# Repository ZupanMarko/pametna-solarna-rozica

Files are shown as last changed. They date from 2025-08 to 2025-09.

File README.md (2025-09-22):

# Pametna solarna rožica
Projekt vključuje izvorne datoteke in programsko kodo za projekt *Pametna solarna rožica* iz Poletne šole strojništva 2025.
Gre za napravo, ki sledi soncu za optimalni izkoristek sončnih celic na vrhu. Rožica vključuje baterijo in vezje za hitro polnjenje mobilnega telefona.

<p align="center">
  
  <video src="https://github.com/user-attachments/assets/c149758f-b2a8-4514-8fbe-24bb865d2cd1" width="300" controls style="display:inline-block; vertical-align:middle;"></video>
</p>

Projekt vključuje:
* STEP datoteke sestavnih delov
* Altium in gerber datoteke tiskanin
* programsko kodo
* tabelo vseh sestavnih delov (BOM)

<p align="center">
  Untitled Diagram drawio
</p>

# Kosovnica

| Količina | Naziv | Tip / specifikacija | Opombe | Povezava |
|---|---|---|---|---|
| 1x | Solarni panel | 25 W, plastičen, 18 V | Uporaba na prostem | [link](https://a.aliexpress.com/_EzS1qQS) |
| 1x | Li-Ion celica | 18650, 3.7 V | Brez zaščite, potreben BMS | [link](https://a.aliexpress.com/_EvOZci2) |
| 1x | Arduino Nano | ATmega328P, USB Mini | Klon, 5 V | [link](https://a.aliexpress.com/_Ez3uUz9) |
| 1x | Servo motor | 9 g, 180° | Klasičen RC mikro servo | [link](https://a.aliexpress.com/_EwxFJdM) |
| 1x | Servo motor (kontinuirni) | 9 g, 360° | Kontinuirna rotacija | [link](https://a.aliexpress.com/_EwxFJdM) |
| 1x | MPPT regulator | 18 V vhod | Za polnjenje 1S baterije | [link](https://a.aliexpress.com/_EH76ZsS) |
| 1x | Boost pretvornik | DC–DC step-up | 5–12 V izhod | [link](https://a.aliexpress.com/_Ev8sKLp) |
| 1x | BMS modul | 1S (3.7 V) | Zaščita pred prenapetostjo/praznjenjem | [link](https://a.aliexpress.com/_EJhuM38) |
| 1x | USB modul | QC 3.0 fast charge | 5–12 V izhod | [link](https://a.aliexpress.com/_EI1u6Ka) |
| 4x | Fotoupor | GL5516 | 5–10 kΩ (odvisno od svetlobe) | [link](https://a.aliexpress.com/_EzRV2TM) |
| 1x | Kontaktni konektor | 2-pinski | Za povezavo napajanja | [link](https://a.aliexpress.com/_Ex5KoGA) |
| 1x | Nosilec baterije | 1x 18650 | S kabli | [link](https://a.aliexpress.com/_EykRIGO) |
| 2x | Terminal | Vijak M3 | Pritrditev žic | [link](https://a.aliexpress.com/_EGEYttG) |
| 1x | Stikalo | Mini toggle | ON/OFF | [link](https://a.aliexpress.com/_EIrwWxU) |
| 4x | Upor | 1 kΩ, 1/4 W | ±1 % | [link](https://a.aliexpress.com/_EH9VMBM) |
| 4x | Vijak | M3×16, inbus glava | | – |
| 2x | Vijak | M3×6, inbus glava | | – |
| 1x | Vijak | M4×30, inbus glava | | – |
| 4x | Matica | M3 | | – |
| 1x | Matica | M4 | | – |
| 4x | Žica tanka | 20 cm, cca. 0.2 mm² | Lahko parica iz UTP kabla | – |
| 2x | Žica srednja | 20 cm, 0.75 mm² | Lahko zvočniški kabel | – |
| 3x | Samolepilna nogica | Silikonska | Za stabilnost | – |

POTREBNA ORODJA:
* 3D tiskalnik in 0,3 kg PLA ali podobnega filamenta
* spajkalnik in spajka
* pištolica na vroče lepilo ali sekundno lepilo
* vrtalnik in sveder 8 mm

OPOMBE:
Za pripravo datotek na 3D tisk se priporoča uporaba slicerja PrusaSlicer, saj lahko direktno uvozi step datoteke.
Za naročilo obeh tiskanih se priporoča JLCPCB zaradi nizke cene in hitre dostave.

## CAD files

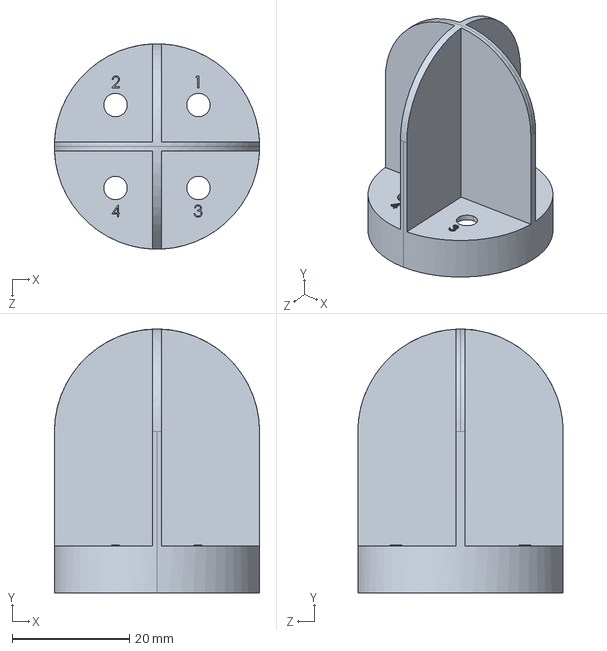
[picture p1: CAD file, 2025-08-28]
STEP datoteke/Sencnik.STEP
35.0 x 45.0 x 35.0 mm

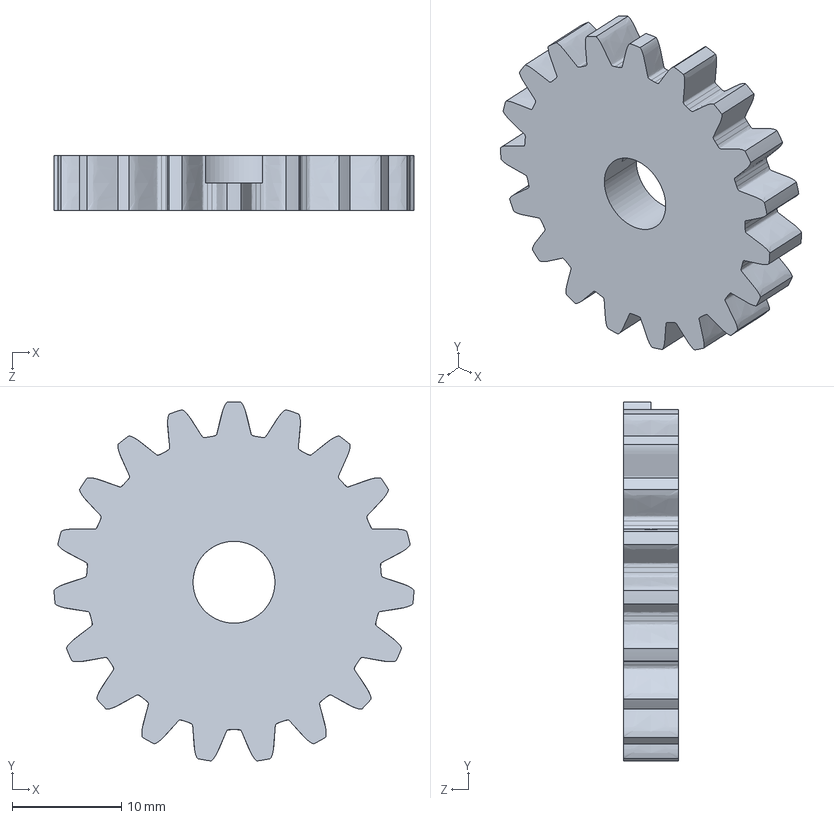
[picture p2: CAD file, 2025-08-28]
STEP datoteke/Zobnik_vrtilni.STEP
33.0 x 32.9 x 5.00 mm

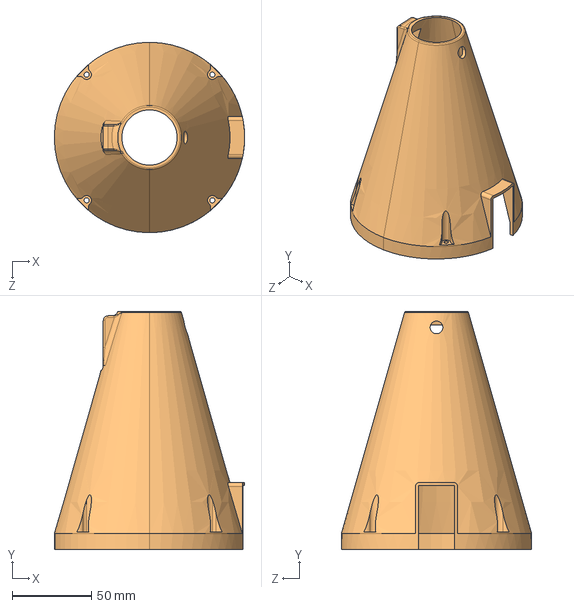
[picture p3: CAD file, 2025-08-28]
STEP datoteke/Telo.STEP
120.0 x 150.0 x 120.0 mm

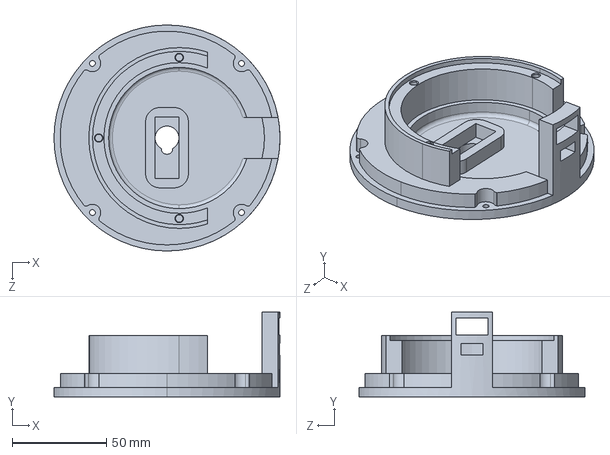
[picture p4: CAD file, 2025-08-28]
STEP datoteke/Stojalo.STEP
120.0 x 45.0 x 120.0 mm

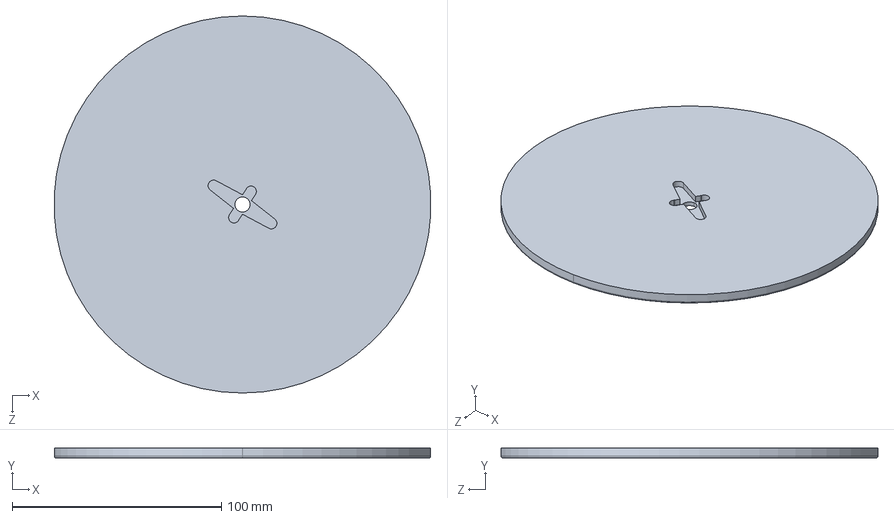
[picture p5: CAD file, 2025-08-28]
STEP datoteke/Stojisce.STEP
179.7 x 5.00 x 180.0 mm

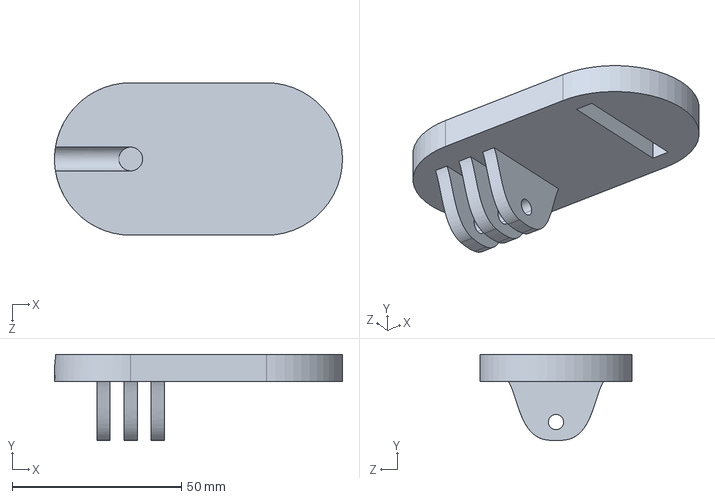
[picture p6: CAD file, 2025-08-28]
STEP datoteke/Gnani_zobnik_drzalo.STEP
85.0 x 25.5 x 45.0 mm

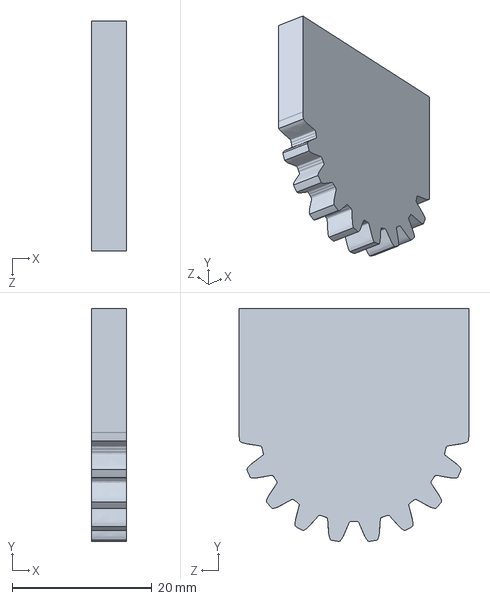
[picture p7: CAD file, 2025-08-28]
STEP datoteke/Zglob_celica_zobnik.STEP
5.00 x 33.4 x 33.0 mm

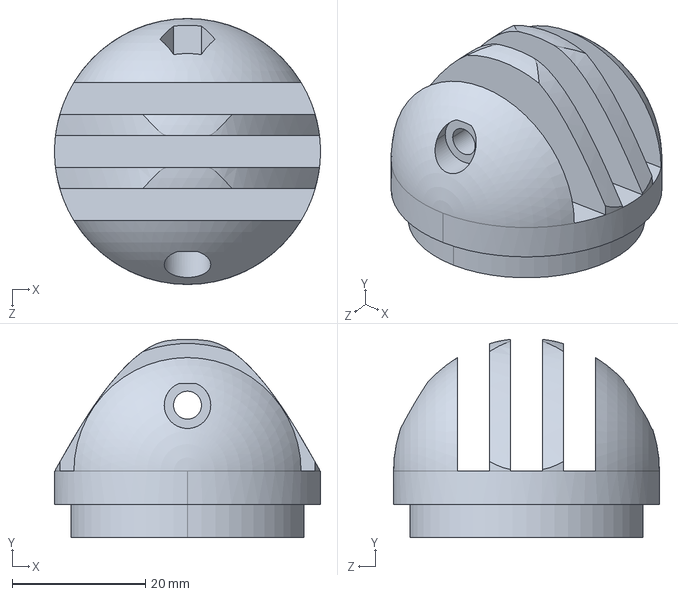
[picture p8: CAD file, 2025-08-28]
STEP datoteke/Zglob_telo.STEP
40.0 x 29.8 x 40.0 mm

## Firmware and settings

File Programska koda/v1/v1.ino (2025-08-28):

//Define sensor pins
#define sensUL A1
#define sensUR A0
#define sensBL A3
#define sensBR A2

//Define servo pins
#define servoRotation 7
#define servoTilt 6

//Include libraries
#include <Servo.h>
Servo Tilt;
Servo Rotation;

//Activate debug mode
bool debug = true;


//----------------------------------------------------------------------------
//Parameters
int startAngle = 150;
long currentAngle = startAngle;
const int tiltStep = 5;
const int tiltTolerance = 5;
const int rotationTolerance = 5;
const int rotationTime = 45;

//Limits
const int maxAngle = 200;
const int minAngle = 20;
//-----------------------------------------------------------------------------
//Function definitions
void tilt(int phi){
  int angle = (float(phi)/180*1000+1000);
  Tilt.writeMicroseconds(angle);

}

void right(){
  Rotation.write(0);
  delay(rotationTime);
  Rotation.write(90);
}

void left(){
  Rotation.write(180);
  delay(rotationTime);
  Rotation.write(90);
}

void up(){
  currentAngle = constrain(currentAngle + tiltStep, minAngle, maxAngle);
  tilt(currentAngle);
}

void down(){
  currentAngle = constrain(currentAngle - tiltStep, minAngle, maxAngle);
  tilt(currentAngle);
}


void setup() {
  Serial.begin(9600);
  Rotation.attach(servoRotation);
  Tilt.attach(servoTilt);
  tilt(currentAngle);


}

void loop() {
  float sensUL_value = analogRead(sensUL);
  float sensUR_value = analogRead(sensUR);
  float sensBL_value = analogRead(sensBL);
  float sensBR_value = analogRead(sensBR);
  	
  if(debug){
    Serial.print("Sensor UL: ");
    Serial.println(sensUL_value);
    Serial.print("Sensor UR: ");
    Serial.println(sensUR_value);
    Serial.print("Sensor BL: ");
    Serial.println(sensBL_value);
    Serial.print("Sensor BR: ");
    Serial.println(sensBR_value);
  }

  //Calculate averages
  float avgTop = (sensUL_value + sensUR_value)/2.0;
  float avgBottom = (sensBL_value + sensBR_value)/2.0;
  float avgLeft = (sensUL_value + sensBL_value)/2.0;
  float avgRight = (sensUR_value + sensBR_value)/2.0;

  bool tiltNeeded = abs(avgTop - avgBottom) > tiltTolerance;
  bool rotationNeeded = abs(avgLeft - avgRight) > rotationTolerance;

  if(tiltNeeded || rotationNeeded){
    if(tiltNeeded){
      if(avgTop > avgBottom){
        up();
      } else{
        down();
      }
    }
    if(rotationNeeded){
      if(avgRight > avgLeft){
        left();
      } else{
        right();
      }
    }
  } else{
    delay(60000);
  }

  delay(500);

}

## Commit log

2025-08-28 Initial file commit
    [Gnani_zobnik_drzalo.STEP, Sencnik.STEP, Stojalo.STEP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]
2025-08-28 Update README.md
    dodan usb fast charge
2025-08-28 dodan gerber
    dodane gerber datoteke obeh tiskanin
2025-08-28 Add files via upload
    dodane Altium datoteke
    [Solarna rozica.PrjPcb, glavni_Fastcharge.PcbDoc, sencnik.PcbDoc]
2025-08-29 kicad board converted from altium
    [Solarna rozica.kicad_pcb]
2025-08-29 New Altium 2 KiCad conversion
    [Solarna rozica.PrjPcb, Solarna rozica.kicad_pcb, glavni_Fastcharge-PcbDoc.kicad_pcb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]
